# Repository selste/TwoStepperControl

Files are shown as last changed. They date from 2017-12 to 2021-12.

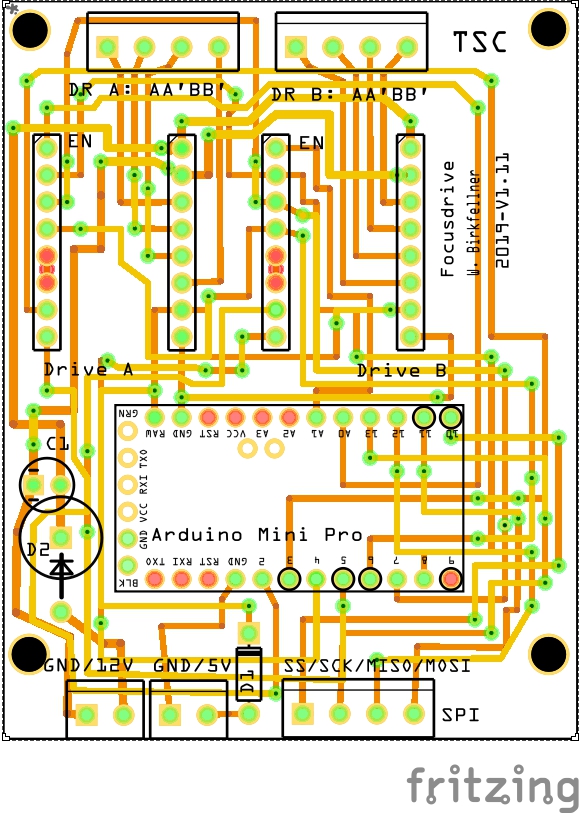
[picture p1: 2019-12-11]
Hardware/4_FocusMotors/MotorBoard_pcb.jpg

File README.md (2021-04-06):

# TwoStepperControl

## Introduction
TSC (TwinStepperControl) is a software project by Wolfgang Birkfellner and Steffen Elste to realize an open integrated control system for large and heavy astronomical telescopes. The basic idea is to use a Raspberry Pi to control a telescope and to provide basic autoguiding functionality without additional external computers. As Raspian is not an RTOS, it cannot control stepper drivers directly like a microcontroller; therefore, extra hardware is necessary which receives basic parameters (number of steps, velocity, acceleration) from the software. We are currently using AMIS 30543 bipolar driver boards with 3A maximum current per coil and a maximum voltage of 30 V.

## Features
TSC basically provides the following functionality
- Telescope tracking and GOTO using internal catalogs for german equatorial and fork mounts in the higher range - up to NEMA 34
steppers are used
- Telescope control via LX200 - both USB/Ethernet and WLAN are supported. In the absence of a WLAN-access point, TSC opens a WLAN network of its own to connect to tablets, cell phones and other computers. Namely, control via SkySafari aon iOS and Android is provided.
- Remote control via VNC (Virtual Network Clients).
- DSLR control including dithering.
- Support for two additional focuser motors.
- Free customization of drives and gears with microstepping ratios between 1/128 and 1/4.
- Image acquisition and autoguiding from guiding cameras via INDI.
- Integrated plate solving via local instalation of Astrometry.net
- Autoguiding integrated on the controller.
- ST4 is also supported

## Documentation
Because we - not intentionally - messed this up a bit in the past we're setting up a dedicated repository/site for documentation:
[TwoStepperControl Documentation](https://tscatm.wordpress.com/)
Please also take a closer look at the manual, which covers all aspects of usage and assembly. However, with the switch to the AMIS drivers, things are in motion

The [Wiki](https://github.com/selste/TwoStepperControl/wiki) in this repository will henceforth only deal with information regarding compilation (and the setup required) and related stuff.

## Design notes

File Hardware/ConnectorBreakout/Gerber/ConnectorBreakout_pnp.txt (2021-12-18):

*Pick And Place List
*Company=
*Author=
*eMail=
*
*Project=ConnectorBreakout
*Date=19:27:29
*CreatedBy=Fritzing 0.9.9b.2021-09-22.CD-348-0-f0af53a9
*
*
*Coordinates in mm, always center of component
*Origin 0/0=Lower left corner of PCB
*Rotation in degree (0-360, math. pos.)
*
*No;Value;Package;X;Y;Rotation;Side;Name
1;;;25.3563;-26.8719;0;Bottom;Hole52
2;;;11.3863;-26.8719;0;Bottom;Hole59
3;;;43.1363;-26.8719;0;Bottom;Hole33
4;;;32.9763;-26.8719;0;Bottom;Hole46
5;;;8.84633;-26.8719;0;Bottom;Hole61
6;;;54.5433;-23.1002;0;Bottom;Hole14
7;;;24.0863;-26.8719;0;Bottom;Hole49
8;;THT;34.1804;-7.35216;90;Bottom;AA' BB'2
9;;;20.3043;-42.1188;0;Bottom;Via8
10;;;57.1063;-26.8719;0;Bottom;Hole23
11;;;7.57641;-26.8719;0;Bottom;Hole60
12;;;6.30641;-26.8719;0;Bottom;Hole62
13;;;1.2265;-26.8719;0;Bottom;Hole83
14;;;36.7863;-26.8719;0;Bottom;Hole38
15;;THT;13.9033;-14.2102;90;Bottom;    
16;;;38.0563;-26.8719;0;Bottom;Hole36
17;;;20.2811;-14.2171;0;Bottom;Via16
18;;;34.2463;-26.8719;0;Bottom;Hole41
19;;;54.5663;-26.8719;0;Bottom;Hole25
20;;;3.75476;-37.0411;0;Bottom;Via6
21;;;11.3714;-37.0411;0;Bottom;Via5
22;;THT;34.2464;-42.1118;90;Bottom;   
23;;THT;34.2035;-35.2538;90;Bottom;AA' BB'
24;;;20.2811;-9.13932;0;Bottom;Via15
25;;;2.47336;-24.3702;0;Bottom;Hole15
26;;;8.82328;-20.5602;0;Bottom;Hole9
27;;THT;50.7333;-14.2102;90;Bottom;   
28;;;11.3482;-9.13932;0;Bottom;Via13
29;;THT;52.0033;-16.7502;90;Bottom;   
30;;;38.0333;-23.1002;0;Bottom;Hole12
31;;;58.3763;-26.8719;0;Bottom;Hole21
32;;;43.1779;-47.5283;0;Bottom;TXT2
33;;;48.2163;-26.8719;0;Bottom;Hole34
34;;;30.4364;-51.0018;0;Bottom;Hole4
35;;;30.4363;-26.8719;0;Bottom;Hole42
36;;;3.76641;-26.8719;0;Bottom;Hole86
37;;;30.4595;-38.2636;0;Bottom;Via11
38;;;63.4563;-26.8719;0;Bottom;Hole18
39;;THT;35.4933;-16.7502;90;Bottom;   
40;;THT;15.1964;-39.5718;90;Bottom;     
41;;;12.6563;-26.8719;0;Bottom;Hole57
42;;;55.8363;-26.8719;0;Bottom;Hole28
43;;;62.1863;-26.8719;0;Bottom;Hole19
44;;;5.03641;-26.8719;0;Bottom;Hole63
45;;;22.8163;-26.8719;0;Bottom;Hole48
46;;;49.4863;-26.8719;0;Bottom;Hole29
47;;;53.2963;-26.8719;0;Bottom;Hole24
48;;THT;14.1703;-4.81199;90;Bottom;1
49;;;2.49642;-52.2718;0;Bottom;Hole8
50;;;40.5963;-26.8719;0;Bottom;Hole40
51;;THT;34.2233;-14.2102;90;Bottom;   
52;;;46.9463;-26.8719;0;Bottom;Hole31
53;;THT;15.1733;-11.6702;90;Bottom;   
54;;THT;13.9264;-42.1118;90;Bottom;  
55;;;17.7363;-26.8719;0;Bottom;Hole58
56;;;10.1163;-26.8719;0;Bottom;Hole64
57;;;15.1963;-26.8719;0;Bottom;Hole54
58;;;52.0263;-26.8719;0;Bottom;Hole26
59;;;46.9464;-51.0018;0;Bottom;Hole2
60;;;30.4363;-10.3619;0;Bottom;Via19
61;;;41.8663;-26.8719;0;Bottom;Hole35
62;;THT;14.1934;-32.7138;90;Bottom;1
63;;;54.5664;-51.0018;0;Bottom;Hole1
64;;;50.7563;-26.8719;0;Bottom;Hole27
65;;;39.3263;-26.8719;0;Bottom;Hole37
66;;;20.2763;-26.8719;0;Bottom;Hole51
67;;THT;35.5164;-44.6518;90;Bottom;   
68;;THT;50.6904;-7.35216;90;Bottom;AA' BB'1
69;;;44.4063;-26.8719;0;Bottom;Hole32
70;;;35.5163;-26.8719;0;Bottom;Hole39
71;;;20.2764;-48.4618;0;Bottom;Hole5
72;;;2.49641;-26.8719;0;Bottom;Hole85
73;;;14.3707;-45.145;0;Bottom;TXT1
74;;;62.1864;-52.2718;0;Bottom;Hole7
75;;;21.5463;-26.8719;0;Bottom;Hole50
76;;;38.0564;-51.0018;0;Bottom;Hole3
77;;;31.7063;-26.8719;0;Bottom;Hole43
78;;;45.6763;-26.8719;0;Bottom;Hole30
79;;;62.1633;-24.3702;0;Bottom;Hole16
80;;;20.3043;-37.0411;0;Bottom;Via7
81;;;30.4133;-23.1002;0;Bottom;Hole11
82;;THT;50.7135;-35.2538;90;Bottom;AA' BB'
83;;;20.2533;-20.5602;0;Bottom;Hole10
84;;;59.6463;-26.8719;0;Bottom;Hole22
85;;;46.915;-44.6576;0;Bottom;Via9
86;;;30.4363;-16.7559;0;Bottom;Via20
87;;;3.7317;-9.13932;0;Bottom;Via14
88;;THT;50.7564;-42.1118;90;Bottom;   
89;;;8.84642;-48.4618;0;Bottom;Hole6
90;;;27.8963;-26.8719;0;Bottom;Hole45
91;;;26.6263;-26.8719;0;Bottom;Hole47
92;;;29.1663;-26.8719;0;Bottom;Hole44
93;;;46.9233;-23.1002;0;Bottom;Hole13
94;;THT;52.0264;-44.6518;90;Bottom;   
95;;;30.4595;-44.6576;0;Bottom;Via12
96;;;46.915;-38.2636;0;Bottom;Via10
97;;;46.8919;-16.7559;0;Bottom;Via17
98;;;60.9163;-26.8719;0;Bottom;Hole20
99;;;19.0063;-26.8719;0;Bottom;Hole53
100;;;13.9263;-26.8719;0;Bottom;Hole56
101;;;16.4663;-26.8719;0;Bottom;Hole55
102;;;46.8919;-10.3619;0;Bottom;Via18

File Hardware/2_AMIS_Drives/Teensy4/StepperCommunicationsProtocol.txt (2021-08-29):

Communications protocol for the Stepper Drivers of TSC
W. Birkfellner, Aug. 2021, V. 0.1

The stepperboards communicate via USB between the host computer and 
the Teensy 4.0 running the steppers with the AccelStepper library.
so far the commands are transmitted as characters, following the convention:
xyzzzzzz...
where x is a character denoting the action to be taken, y is a number between
0 and 1, and zzzzzz... is a string of bytes that is converted to a long integer. 

An example:
"a1200" sets the acceleration (denoted by 'a') of the second drive ('1' instead 
of '0') to 200 microsteps per second. 

Commands that apply to all drives (such as the request for the drive state) are given without additional bytes

In general, parameters have to be set, then the drive is enabled, and then ist should start. 
Once a motion is finished, the drive is being automatically disabled.

Command set:
0x06 or <ACK>	... responds with an identifier for the drive addressed. Replies are either "TSC_DE" or "TSC_RA". No further parameters are given.
a 		... sets acceleration in msteps/(s*s)
c 		... sets current
e 		... enables the drive; it is automatically activated when an "start drive" command (= 'o') is sent
f		... reports drive conditions. Possible parameters are
			0 = is drive moving
			1 = error on AMIS board reported
			2 = error on SPI settings
			5 = steps carried out so far
			6 = microstepping ratio
			7 = maximum speed in msteps/s 
			8 = acceleration in msteps/(s*s) 
			9 = maximum current per coil in milliAmpere
			10 = number of steps set
m 		... sets microstepping mode for a given drive: 1, 2, 4, 8, 16, 32, 64 and 128 are permitted    
o 		... engages the drive to carry out a defined number of microsteps     
r 		... resets the AMIS via its CLR pin
s 		... sets the number of steps to be carried out
v 		... sets maximum speed in msteps/s      
x 		... stops drive
z		... sets position of stepper to zero

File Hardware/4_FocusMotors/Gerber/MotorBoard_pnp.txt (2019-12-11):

*Pick And Place List
*Company=
*Author=
*eMail=
*
*Project=MotorBoard
*Date=13:08:43
*CreatedBy=Fritzing 0.9.3b.04.19.5c895d327c44a3114e5fcc9d8260daf0cbb52806
*
*
*Coordinates in mm, always center of component
*Origin 0/0=Lower left corner of PCB
*Rotation in degree (0-360, math. pos.)
*
*No;Value;Package;X;Y;Rotation;Side;Name
1;;;7.39582;-60.8985;0;Bottom;Via19
2;;;52.4807;-16.4486;0;Bottom;Via71
3;;;45.9584;-65.5036;0;Bottom;TXT2
4;;THT;9.58283;-2.85951;-90;Bottom;GND/12V
5;;;51.2107;-20.8936;0;Bottom;Via50
6;;;32.1607;-12.6386;0;Bottom;Via64
7;;;12.5126;-48.2445;0;Bottom;Via4
8;;;22.6357;-34.8635;0;Bottom;Via75
9;;;48.6707;-20.8936;0;Bottom;Via56
10;;;27.0808;-22.7985;-90;Bottom;Arduino Mini Pro
11;;;2.95082;-31.0536;0;Bottom;Via13
12;;;14.3807;-32.9586;0;Bottom;Via39
13;;;9.93582;-35.7807;0;Bottom;Via68
14;;;28.3507;-49.4685;0;Bottom;Via27
15;;THT;17.4568;-2.85951;-90;Bottom;GND/5V
16;;;42.3207;-28.5136;0;Bottom;Via47
17;;;16.9207;-58.3585;0;Bottom;Via6
18;;;46.1307;-62.1685;0;Bottom;Via44
19;;THT;4.22083;-46.9285;0;Bottom;EN
20;;;9.30082;-11.0158;0;Bottom;Via69
21;;THT;32.8238;-65.8515;-90;Bottom;DR B: AA'BB'
22;;;49.9407;-12.6386;0;Bottom;Via61
23;;;16.9207;-32.3236;0;Bottom;Via31
24;;;19.4607;-57.0885;0;Bottom;Via15
25;;;2.63332;-66.931;0;Bottom;Hole2
26;;;49.9407;-24.7036;0;Bottom;Via46
27;;;13.7397;-45.6677;0;Bottom;Via2
28;;;8.03082;-19.6236;0;Bottom;Via66
29;;THT;38.5108;-46.9285;0;Bottom;Drive B
30;;;19.4607;-41.8485;0;Bottom;Via38
31;;THT;25.8108;-46.9285;0;Bottom;EN 
32;;;5.53582;-17.0528;90;Bottom;D2
33;;;2.95082;-27.8786;0;Bottom;Via12
34;;THT;33.4588;-2.98648;-90;Bottom;SPI
35;;;46.1307;-36.1335;0;Bottom;Via24
36;;;47.4007;-34.8635;0;Bottom;Via28
37;;;28.3507;-47.5635;0;Bottom;Via30
38;;;15.0157;-55.8185;0;Bottom;Via9
39;;;51.2107;-14.8258;0;Bottom;Via73
40;;;2.31582;-62.1685;0;Bottom;Via43
41;;;51.5358;-8.07351;0;Bottom;Hole3
42;;;46.1307;-10.0986;0;Bottom;Via72
43;;;44.8607;-22.7986;0;Bottom;Via42
44;;;8.03082;-27.2436;0;Bottom;Via65
45;;;47.3698;-49.9384;-90;Bottom;TXT5
46;;;44.5785;-11.3686;0;Bottom;Via70
47;;;23.2707;-12.6386;0;Bottom;Via40
48;;;4.22082;-32.9586;0;Bottom;Via59
49;;;47.4007;-20.2586;0;Bottom;Via57
50;;;6.12582;-50.7385;0;Bottom;Via36
51;;;44.8607;-18.9886;0;Bottom;Via29
52;;THT;15.0438;-65.8515;-90;Bottom;DR A: AA'BB'
53;;;38.5107;-58.3585;0;Bottom;Via5
54;;THT;16.9496;-46.9107;0;Bottom;Drive A
55;;;44.62;-49.1489;-90;Bottom;TXT4
56;;;9.30082;-54.5485;0;Bottom;Via14
57;;;35.3357;-7.55861;0;Bottom;Via55
58;;;12.4758;-53.2785;0;Bottom;Via3
59;;;52.4807;-28.5136;0;Bottom;Via48
60;;;33.4307;-36.1335;0;Bottom;Via21
61;0.1mF;100 mil [THT, electrolytic];4.2265;-24.0437;0;Bottom;C1
62;;;23.9057;-54.5485;0;Bottom;Via33
63;;;41.0507;-32.3236;0;Bottom;Via32
64;;;37.2407;-53.2785;0;Bottom;Via18
65;;;48.6707;-22.7986;0;Bottom;Via41
66;;;37.2407;-25.3386;0;Bottom;Via51
67;;;7.39582;-48.1985;0;Bottom;Via37
68;;;15.6507;-53.9135;0;Bottom;Via11
69;;;39.7807;-25.3386;0;Bottom;Via52
70;;;13.7458;-52.0085;0;Bottom;Via1
71;;;44.8607;-59.6285;0;Bottom;Via23
72;;;49.9407;-33.5936;0;Bottom;Via45
73;;;6.12582;-54.5485;0;Bottom;Via35
74;;;35.3755;-6.81038;0;Bottom;TXT1
75;;;22.0007;-60.8985;0;Bottom;Via20
76;;;1.04582;-57.7235;0;Bottom;Via10
77;;;4.22082;-59.6285;0;Bottom;Via8
78;;;23.9057;-50.7385;0;Bottom;Via34
79;;;34.7007;-26.6086;0;Bottom;Via49
80;;;22.6357;-38.0385;0;Bottom;Via67
81;;;31.5257;-39.3085;0;Bottom;Via25
82;;;25.8107;-4.38361;0;Bottom;Via63
83;;;19.1785;-34.8635;0;Bottom;Via74
84;;;51.5358;-67.0735;0;Bottom;Hole5
85;;;36.6057;-40.5785;0;Bottom;Via26
86;;;49.9407;-17.7186;0;Bottom;Via60
87;;300 mil [THT];23.2708;-6.26311;90;Bottom;D1
88;;;2.53583;-8.07351;0;Bottom;Hole4
89;;;42.1804;-49.1414;-90;Bottom;TXT3

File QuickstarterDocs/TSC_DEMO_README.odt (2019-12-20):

TSC_DEMO.img.gz – what is it?

wbirkfellner@gmail.com – tscatm.wordpress.com

You are reading this because you apparently have received a rather big file called “TSC_DEMO.img.gz”. This is a demonstrator for the free telescope controller software TSC, written for the Raspberry Pi family of single board computers.

This is an image of a 16GB SD-card holding the minimum libraries and a binary copy of the TSC software. It is a demonstrator because all necessary tools for modifying TSC or building the hardware associated with it were removed for saving space. Without the hardware, TSC is a brain without limbs, and therefore its functionality is very limited.

Things that can be done:

- Get an idea of the internal functionality of TSC.
- See how TSC integrates into your local network/WLAN.
- Check how it connects to your favourite planetarium program. Denote that a serial connection via USB is only available with the TSC hardware, but connection via WLAN (e. g. via SkySafari or Kstars) is possible. Of course TSC does not move, but if you Sync on an object using the internal catalog, you can at least see little crosshairs hopping around.
- Check whether your camera connects to the internal camera interface of TSC for use with the internal guider or (in the near future) internal platesolving, a functionality under development for use with the new Raspberry Pi 4 family of SBCs.

How to make an SD card:

- Uncompress the TSC_DEMO.img.gz image. Make sure that you have enough space available on your harddisk, and yes, this takes a while. On Linux, you can simply double-click TSC_DEMO.img.gz. On other operating systems, the procedure is similar.
- Make a physical copy on a (fast) 16 GB minimum SD card. On Linux (or Raspian), this is done by typing: sudo dd if=<location of input file> of=<device to write to> bs=8M status=progress <device to write to> is the physical location of your SD-card; with an external card reader, this is usually a /dev/sd… device, an internal card reader can often be found at /dev/mmcblk0. You can also use the Disk Image Writer that comes for instance with Ubuntu. Writing an SD-card is of course also feasible on other operating systems; for details, check for instance: https://learn.sparkfun.com/tutorials/sd-cards-and-writing-images/all
- Put the SD card into at least a Raspberry Pi 3B, connect a mouse and a HDMI monitor and boot it.
- Synchronize your clock, either by using SkySafari (sse instructions below), or by connecting your Raspberry Pi to an Ethernet cable and wait until a time server signal is received. You can also set date and time manually by closing TSC using the Exit button, opening a terminal by pressing <Ctrl-Alt-T> and typing: sudo date -s "20 DEC 2019 18:00:00" – of course with the right time and date. Restart TSC with the TSC desktop icon after that.

What you will see:

- A warning that no drives are connected. This is ok as no drives are connected.
- After confirmation, TSC will come up. It spawns an autonomous network called TSCHotspot; the password is TSCRaspi – use these credentials to access the LX200 client client via your planetarium program. The IP address to connect to is 192.168.50.5, the Port is 49152. Set your location in the Location tab, store it using Store Data and make sure that your system clock is correct – the TSC hardware has a buffered real-time clock, you don’t have one. On SkySafari, you can synchronize by sending time and location; make sure that the checkbox Allow time/position from LX200 is checked in the Location tab of TSC.
- Plug in your camera and go to the CCD tab. Select your camera vendor, click Start INDI Server and Connect. In the next tab (called Guiding), you can now Expose an image an see whether something comes in there.

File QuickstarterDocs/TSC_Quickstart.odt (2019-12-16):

Starting with TSC – the bare minimum guide

W. Birkfellner, wbirkfellner@gmail.com

tscatm.wordpress.com

Let us assume that the TSC hardware is assembled and powered up – so here is a very short and minimalistic guide to get started with TSC.

1: Connect your drives

TSC operates bipolar stepping motors. These have two coils and four wires running out. Some have more, and then reading the documentation for the drives is recommended. Let us call the wire pairs AA’ and BB’. In order to find out which wires form a pair, one needs a documentation or a multimeter. A pair of wires always has a relative resistance of almost 0 Ohm. Connect these pairs to the terminals on the driver boards. If you figure out at a later stage that your drives are turning in the wrong direction, you may need to permutate A and A’ or B and B’ - or both. Fig. 1 shows the location of the terminal on the AMIS board.

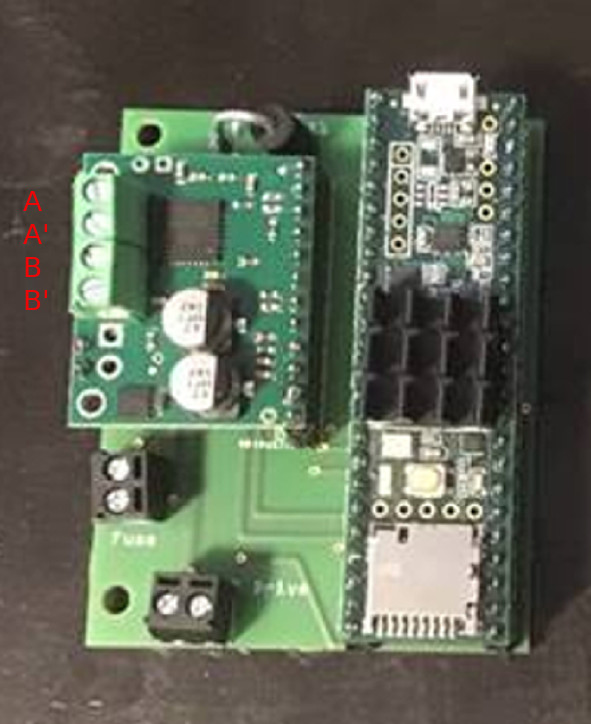
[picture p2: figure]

| Fig. 1: Connection terminals for the four wires of a bipolar stepper on one of the AMIS boards. This is an older board with a Teensy 3.5 as a microcontroller.

2: Set up current and gear ratios:

TSC can handle up to 3A per coil and a motor voltage up to 30V (the latter affects the maximum end speed). Your motor also has a maximum current rating. Do not set the current above 70% of this rating (for the time being). Fig. 2 shows how to adjust the current in the Settings dialog of TSC for both the right ascension (RA) and Declination drive. Also set an acceleration A in microsteps/second². 5000 msteps/s² is a good starting point. Set the gear and microstepping ratios and press Store gear data. A recommended setting for microsteps is 1/128 for Track and Guide, 1/16 for Move and 1 /4 for GoTo. Uncheck Northern Hemisphere if you are on the southern hemisphere. Leave Enable Meridian Flip disabled, even if you have a German equatorial, for the time being.

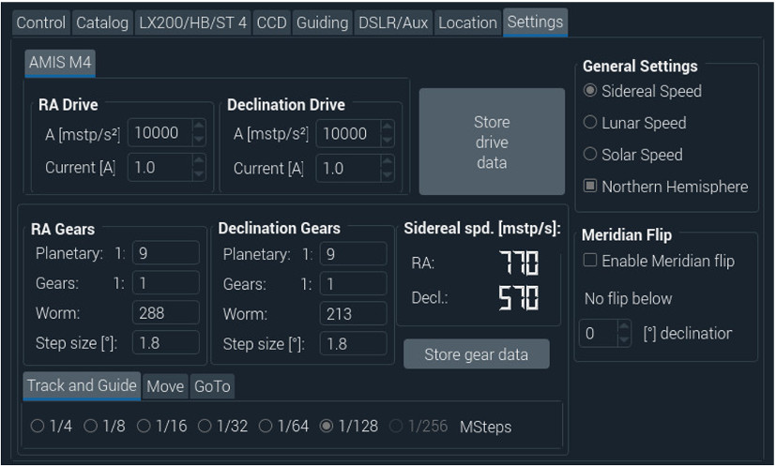
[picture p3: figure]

Fig. 2: Adjustment of current, gears and microsteps for basic stepper operation. Start with 70 % of your rated stepper coil current. A value of 5000 microsteps/s² is a good value for the acceleration A of the steppers. Press Store drive data once you have found your settings. Leave the Enable Meridian Flip check box unchecked for the time being. Enter the gear ratio for you Planetary drive, your intermediate Gear (e. g. belts) and the number of teeth on you Worm wheel. Also enter the step size for a full step and the microstepping ratios for Tracking and Guide-ing, handbox Moves and GoTo. Press the Store gear data button once you are done.

3: Set up speeds and do fine adjustments:

Now, your mount should be ready for first moves using the direction buttons on the main screen (Fig. 3). Set V-Move to 50 (multiples of sidereal speed) and V-GoTo to 100. Press the Store Speeds button. Move the drives with Up, Down, Left and Right. Now fine adjust currents and maximum speed. A whining sound at maximum speed accompanied by no motion means that the speed is too high for this setup – reduce it. A rough motion of the drive, accompanied with heating the drive up, means that the current is to high – lower it. An irregular motion, accompanied by crackling sounds, means that the torque is too low and the motor loses steps – increase the current, but not beyond the maximum rating of the drive. An optimal setting is found when the drives operate quietly with the minimum current needed. Repeat this until the mount moves smoothly. Also check the maximum GoTo speed V-GoTo by setting V-Move to the same value – and always Store Speeds.

4: Check directions

Grossly point your scope to the south horizon using a level and a compass; if you have a German equatorial, make sure that it’s position (left or right of pier) is also indicated in the GEM left of pier checkbox (Fig. 3). Make sure that the hemisphere you are on (north or south) is indicated properly in the Settings (Fig. 1). If a press on the Right button moves the scope left (or if Up and Down are reversed) – go back to 1.) and permutate A with A’ or B with B’ or both.

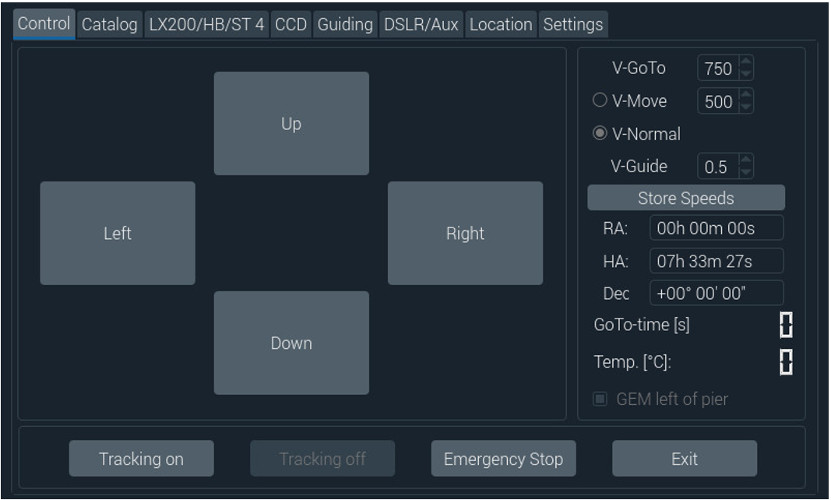
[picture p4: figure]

| Fig. 3: The main screen – adjust your desired speeds for motion (V-Move) and GoTo (V-GoTo) and fine tune your motor current. Don’t forget to Store Speeds if you changed them. The speed is selected with the radiobuttons left of V-Normal and V-Move. The direction buttons are latching – press them a second time to stop a motion. If you cannot enter a current or set a speed, then the drive or speed is active. Use Tracking off button to stop the mount compensating Earth’s rotation if you want to edit the RA-drive settings. Uncheck V-Move to change the speed.

5: Enable meridian flip (if needed)

If you have a German equatorial (GEM), point your scope to the south horizon, make sure that the scope position left/right of the pier matches the GEM left of pier checkbox (Fig. 3) and Enable the Meridian flip in the Settings tab (Fig. 2). Set No flip below to the minimum declination visible from your site (e. g. -42° if you are at a latitude of 48° as shown in Fig. 4).

6: Sync the scope

Make sure your clock is set up properly and your location is entered correctly (Fig. 4).

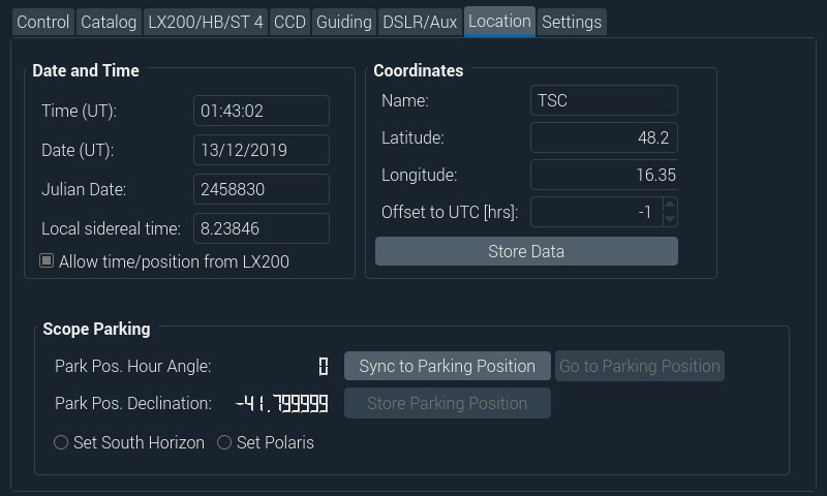
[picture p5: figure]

| Fig. 4: Set your location and make sure that the time (Universal time zone) is set correctly, or let SkySafari do this for you (in this case, the Allow time/position from LX200 checkbox needs to be checked). Don’t forget to Store the Data. If your scope is approximately looking to the south horizon, check Set South Horizon and press the Sync to Parking Position button. If you have not set your time yet and you don’t have SkySafari – connect your Raspberry Pi to a network via Ethernet and wait for an incoming time server signal.

Position your scope to the south horizon grossly using a compass and a level using the direction buttons (Fig. 3) as indicated in Section 4. Set the parking position to the South Horizon in the Location tab and Sync to this Parking Position. Your scope is now approximately synced. Identify a nearby bright star and go to the Catalog tab using the PreciseAlignmentStars or the BrightStars catalogue, click its name and press GoTo (Fig. 5).

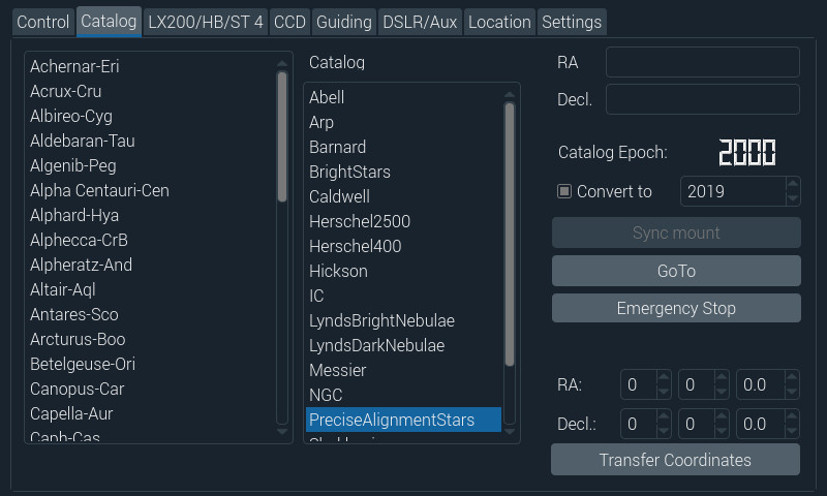
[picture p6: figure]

| Fig. 5: Precise syncing using a bright star and the BrightStars or the PreciseAlignmentStars catalog. Select a star you want to sync on and press GoTo. Fine align the star in the scope using a low to medium power eyepiece and the direction buttons (Fig. 3). Once the star is in the center of the eyepiece, press Sync mount again.

GoTo this bright star and locate it in the eyepiece or finder precisely by fine tuning the scope position with the direction buttons; once it is in the center of the eyepiece of your telescope, Sync the mount again. The scope should now perform GoTo-slews precisely if it is well aligned. Of course these steps can also be carried out through a planetarium program like Kstars.

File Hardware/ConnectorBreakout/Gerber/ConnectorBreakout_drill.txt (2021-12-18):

; NON-PLATED HOLES START AT T1
; THROUGH (PLATED) HOLES START AT T100
M48
INCH
T1C0.039370
T2C0.118110
T100C0.038000
T101C0.039370
T102C0.015748
T103C0.040000
%
T1
X000482Y010579
X011982Y010579
X016982Y010579
X004982Y010579
X008982Y010579
X005482Y010579
X009482Y010579
X024482Y010579
X010982Y010579
X012482Y010579
X003982Y010579
X009982Y010579
X022482Y010579
X006982Y010579
X000982Y010579
X015482Y010579
X019482Y010579
X017982Y010579
X022982Y010579
X021482Y010579
X014482Y010579
X008482Y010579
X016482Y010579
X021982Y010579
X018982Y010579
X017482Y010579
X001482Y010579
X012982Y010579
X013482Y010579
X020982Y010579
X023482Y010579
X007982Y010579
X011482Y010579
X002482Y010579
X004482Y010579
X024982Y010579
X006482Y010579
X007482Y010579
X002982Y010579
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

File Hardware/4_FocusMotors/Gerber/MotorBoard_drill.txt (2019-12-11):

; NON-PLATED HOLES START AT T1
; THROUGH (PLATED) HOLES START AT T100
M48
INCH
T100C0.015748
T101C0.038000
T102C0.040000
T103C0.035000
T104C0.042000
T105C0.129921
%
T100
X013161Y014225
X008661Y023975
X006161Y021225
X006661Y012725
X020661Y006475
X007550Y013725
X009411Y021475
X002411Y021475
X000411Y022725
X011161Y018725
X020661Y011225
X003161Y010725
X003161Y007725
X007661Y022475
X013911Y002975
X000911Y024475
X002911Y023975
X019661Y009725
X014661Y009975
X001661Y012975
X020161Y008225
X004926Y018993
X001161Y010975
X004911Y020975
X017661Y007475
X005911Y021975
X005661Y012975
X020161Y005836
X008911Y013725
X008911Y014975
X019161Y008975
X012661Y004975
X016661Y011225
X001661Y023475
X015161Y022975
X005409Y017979
X002411Y019975
X018161Y003975
X018161Y024475
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

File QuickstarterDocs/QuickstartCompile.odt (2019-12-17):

How to compile TSC

W. Birkfellner

wbirkfellner@gmail.com

Let us assume you have a recent SD-card in the developer version – that is with all software installed for programming and building TSC; and let us assume that you have at least a Raspberry Pi 3 B+, as compiling the C++-sourcecode can be cumbersome.

- Download all data from https://github.com/selste/TwoStepperControl
- Go to you Downloads folder and extract the .zip file to /home/pi
- Open TwoStepperControl-master/C++Source/qdarkstyle and
- right-click rc.tar and select Extract here – see also Fig. 1. A new folder rc should become visible. These are the resources for the stylesheet defining the user interface
- Open TwoStepperControl.pro by double clicking it in TwoStepperControl-master/C++Source/. QtCreator will be invoked.
- Select Release and click on Build › Build project “TwoStepperControl”
- Ignore all warnings and wait until the compilation process is done as indicated by the progress bar in the lower right hand side. (Fig. 2).
- Go one directory up to TwoStepperControl-master/ and copy the Catalogs folder to the build-TwoStepperControl-Desktop-Release folder (Fig. 3).
- TSC can be started by double clicking the TSC icon on the desktop.

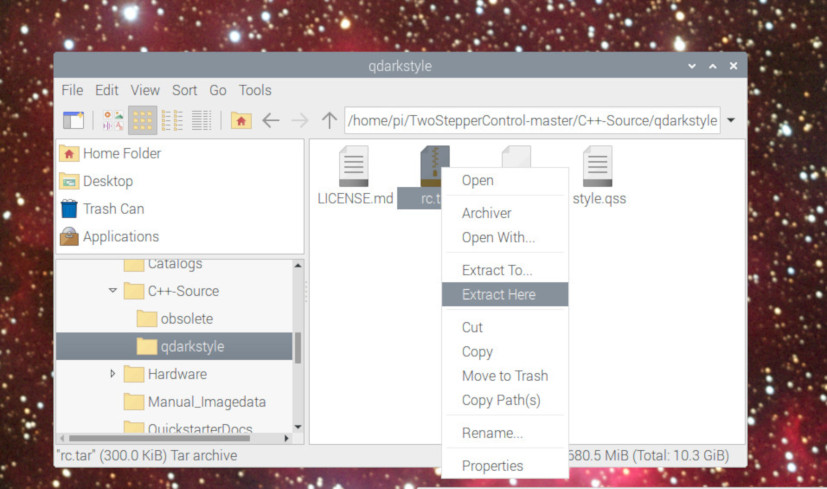
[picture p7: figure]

| Fig. 1: Extraction of the rc-folder from rc.tar – a new folder named rc will appear.

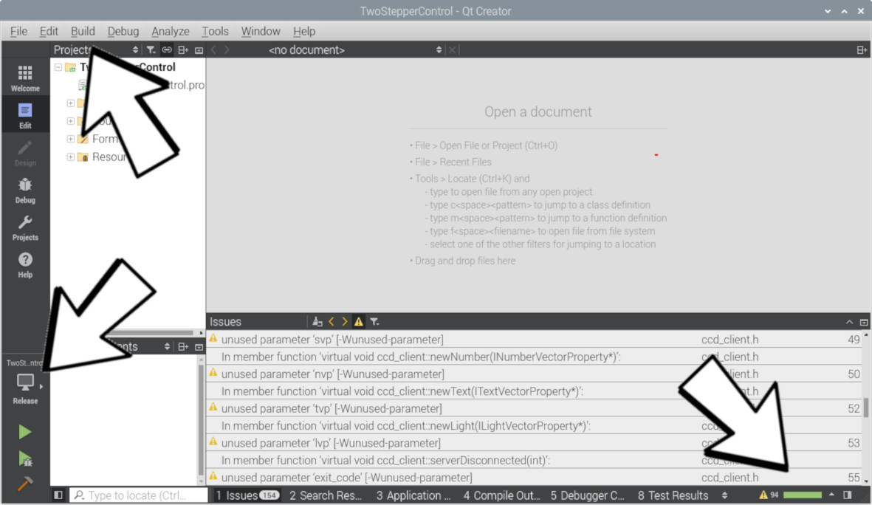
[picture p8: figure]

| Fig. 2: Compilation with QtCreator. Open TwoStepperControl.pro in the C++Source folder and take care that you are in Release mode (lower left hand) and start the compilation process in the Build menu.

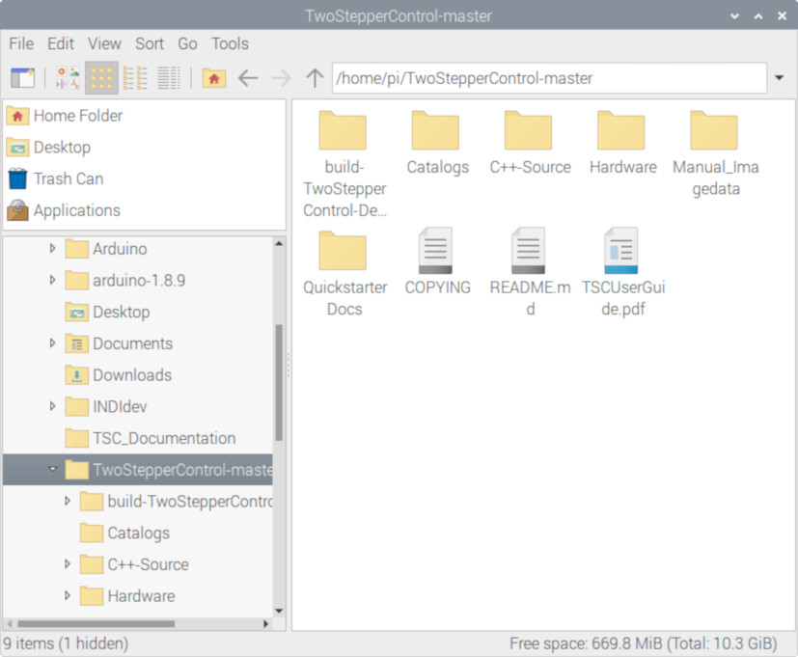
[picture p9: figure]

| Fig. 3: Copy the Catalogs folder to build-TwoStepperControl-Desktop-Release.

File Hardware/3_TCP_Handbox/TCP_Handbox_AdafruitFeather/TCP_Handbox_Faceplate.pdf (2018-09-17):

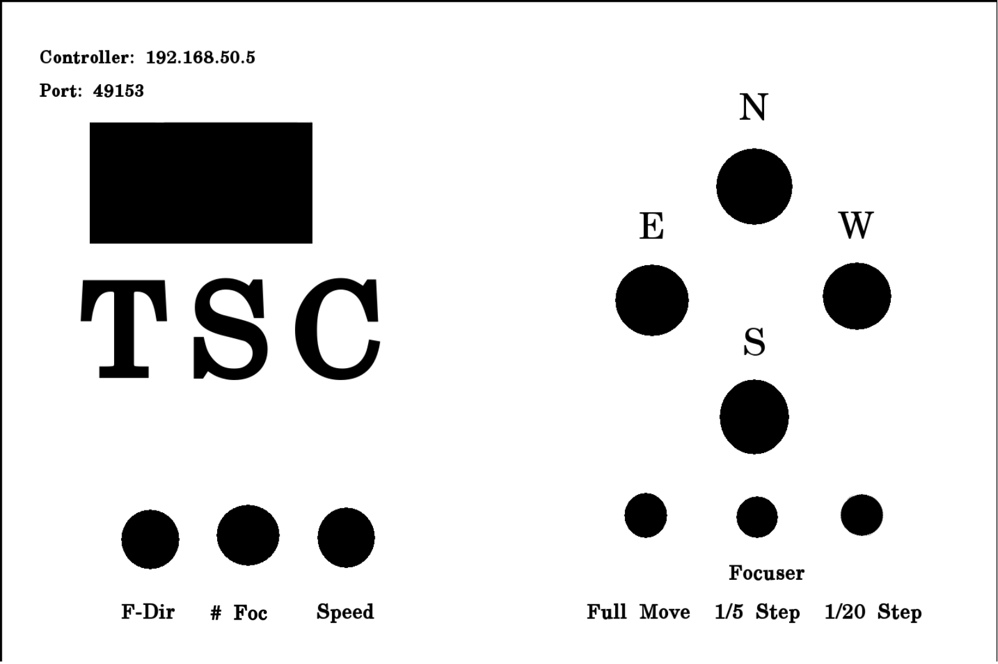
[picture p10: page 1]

# Foc

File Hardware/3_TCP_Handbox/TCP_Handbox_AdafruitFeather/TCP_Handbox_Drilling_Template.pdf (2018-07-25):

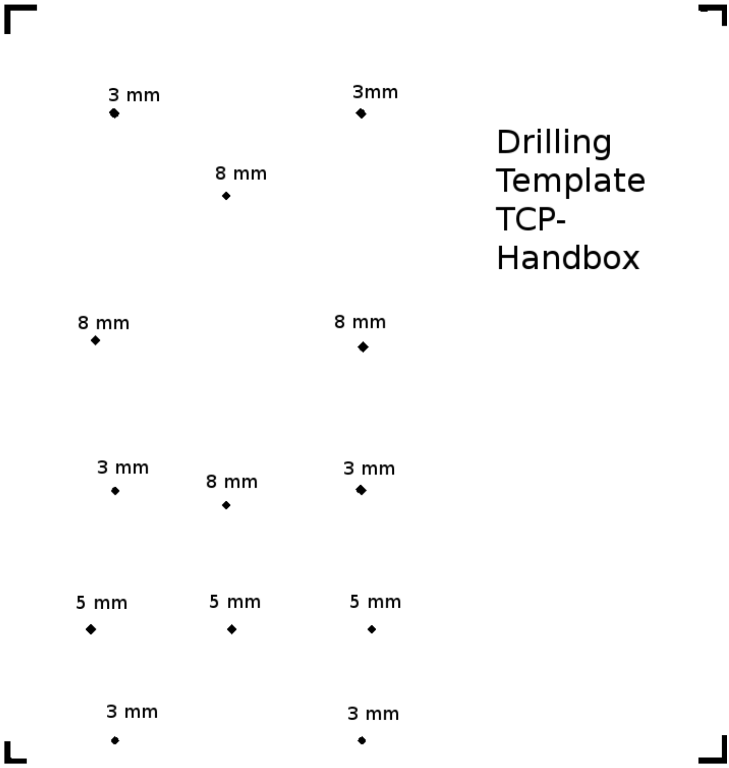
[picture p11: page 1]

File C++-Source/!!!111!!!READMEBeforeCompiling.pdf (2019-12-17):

### How to compile TSC

W. Birkfellner
wbirkfellner@gmail.com

Let us assume you have a recent SD-card in the developer version – that is with all software installed for programming and building TSC; and let us assume that you have at least a Raspberry Pi 3 B+, as compiling the C++-sourcecode can be cumbersome.
- Download all data from https://github.com/selste/TwoStepperControl
- Go to you Downloads folder and extract the .zip file to /home/pi
- Open TwoStepperControl-master/C++Source/qdarkstyle and
- right-click rc.tar and select Extract here – see also Fig. 1. A new folder rc should become visible. These are the resources for the stylesheet defining the user interface
- Open TwoStepperControl.pro by double clicking it in TwoStepperControl-master/C+ +Source/. QtCreator will be invoked.

### - Select Release and click on Build › Build project “TwoStepperControl”

- Ignore all warnings and wait until the compilation process is done as indicated by the progress bar in the lower right hand side. (Fig. 2).
- Go one directory up to TwoStepperControl-master/ and copy the Catalogs folder to the build-TwoStepperControl-Desktop-Release folder (Fig. 3).
- TSC can be started by double clicking the TSC icon on the desktop.

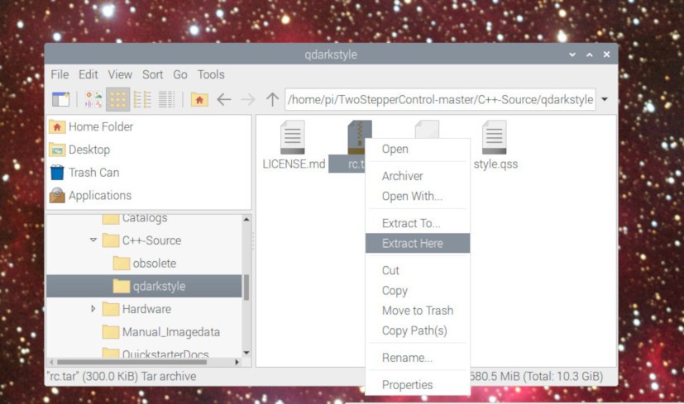
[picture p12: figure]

Fig. 1: Extraction of the rc-folder from rc.tar – a new folder named rc will appear.

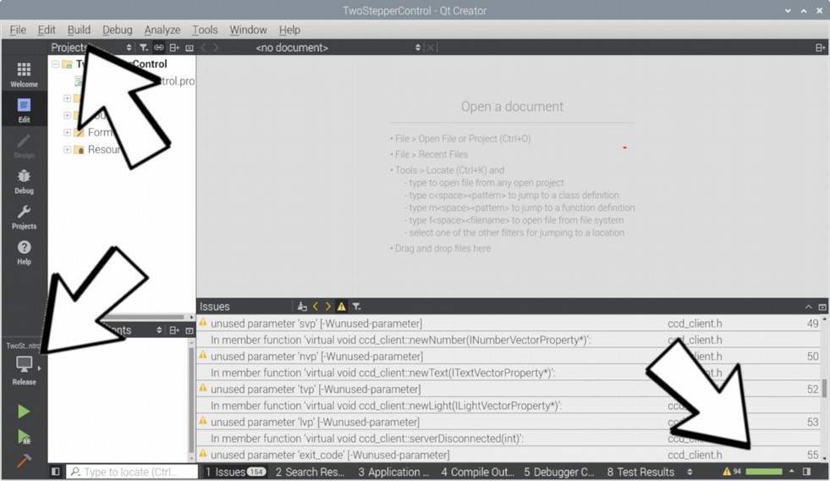
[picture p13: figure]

Fig. 2: Compilation with QtCreator. Open TwoStepperControl.pro in the C++Source folder and take care that you are in Release mode (lower left hand) and start the compilation process in the Build menu.

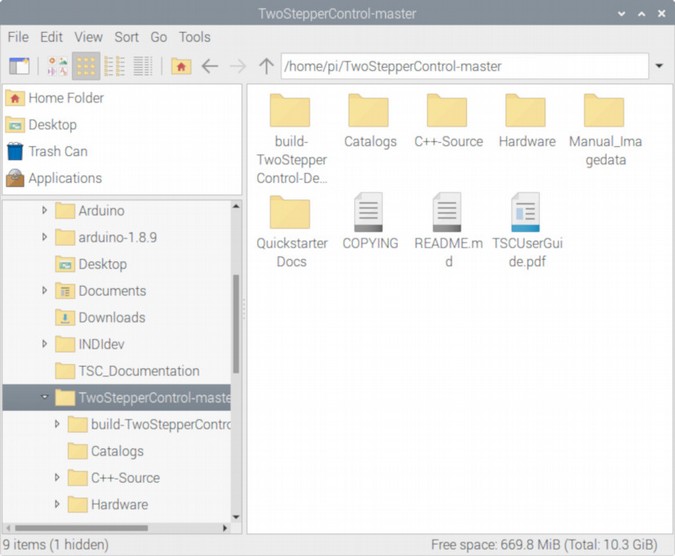
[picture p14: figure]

Fig. 3: Copy the Catalogs folder to build-TwoStepperControl-Desktop-Release.

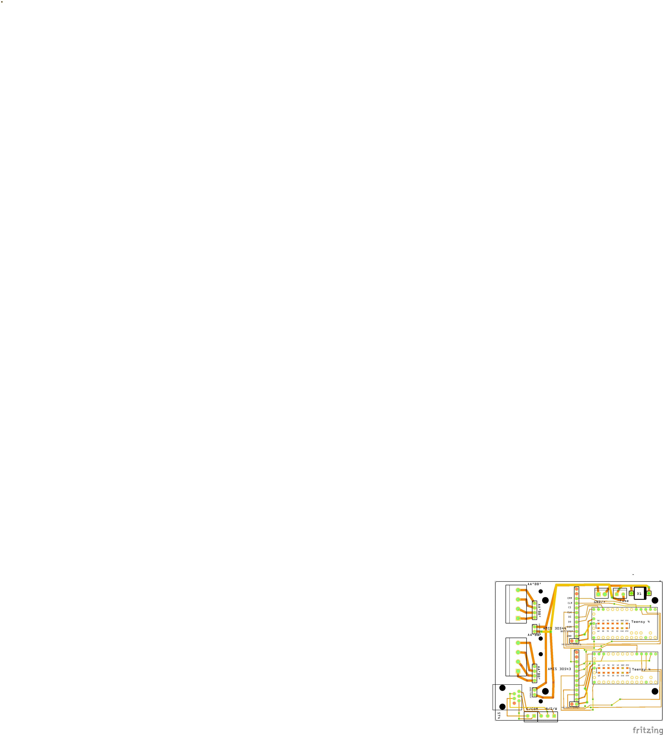
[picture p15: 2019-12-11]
Hardware/2_AMIS_Drives/Teensy4/AMIS30543_Teensy_2_pcb.jpg

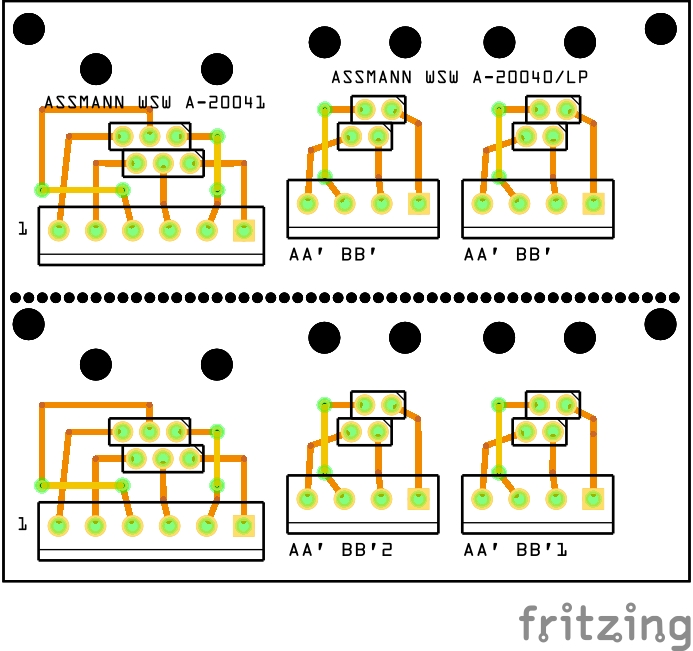
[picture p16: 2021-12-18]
Hardware/ConnectorBreakout/ConnectorBreakout_pcb.jpg

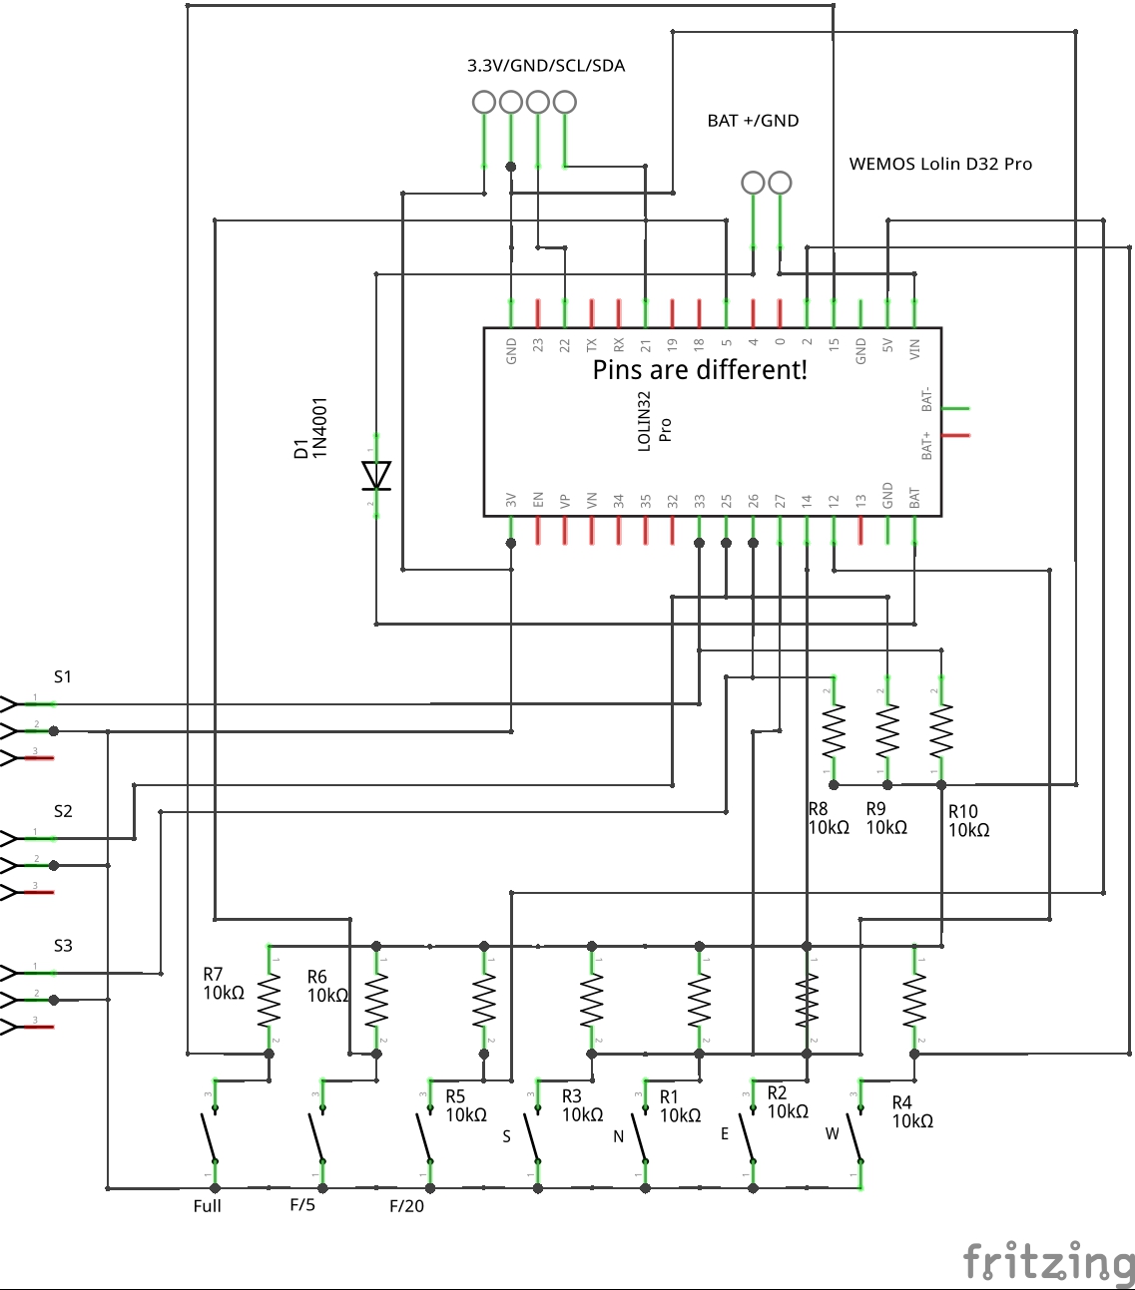
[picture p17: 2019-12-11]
Hardware/3_TCP_Handbox/TCP_Handbox_LOLIND32Pro/TCP_Handbox_schem.jpg

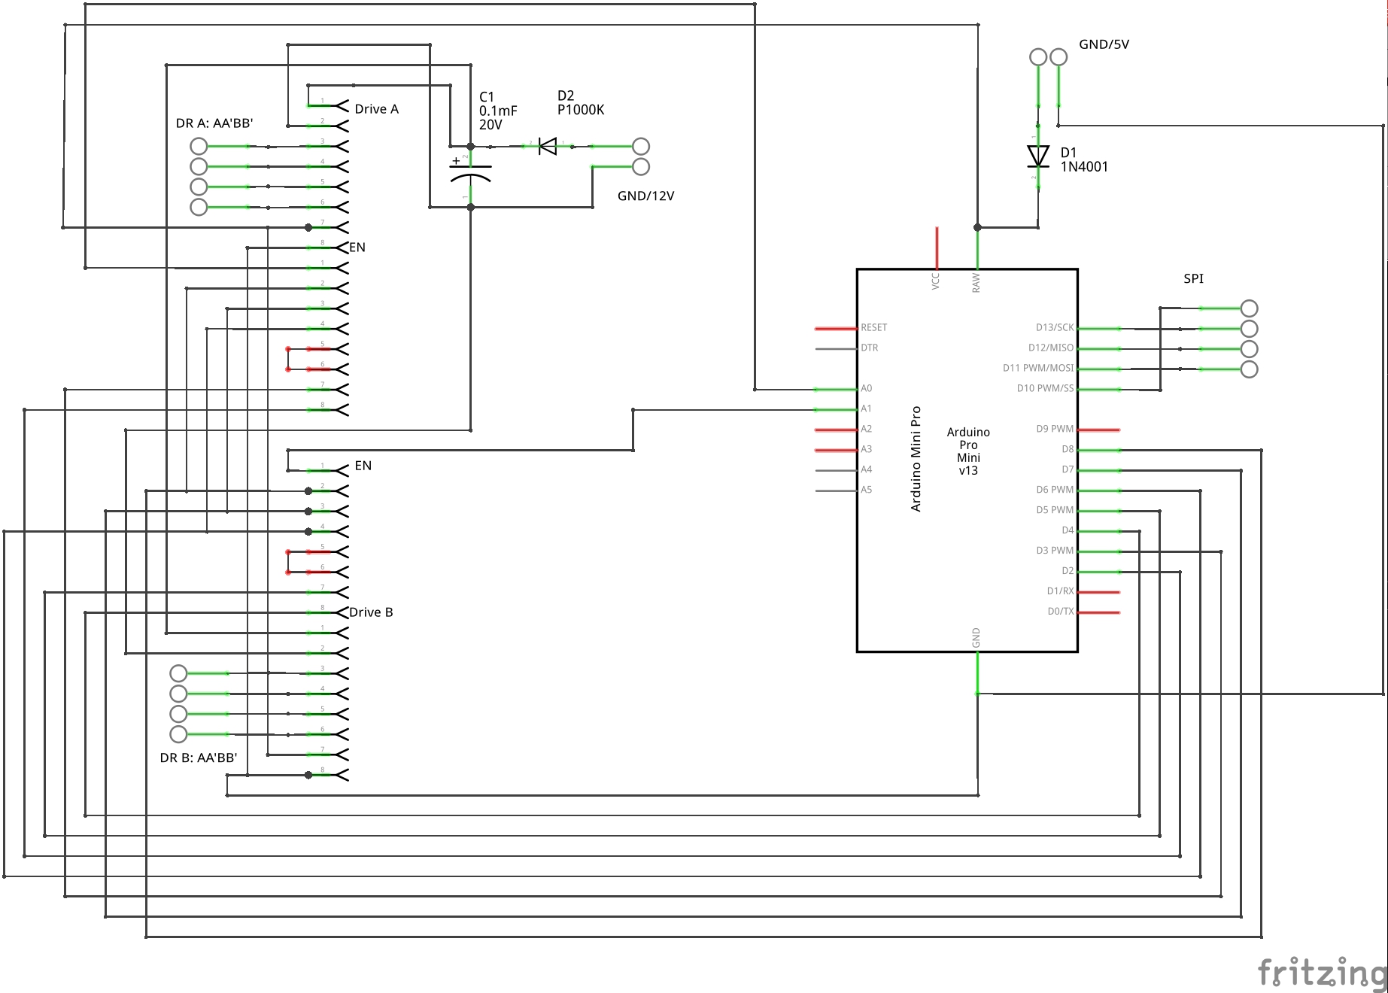
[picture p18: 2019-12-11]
Hardware/4_FocusMotors/MotorBoard_schem.jpg

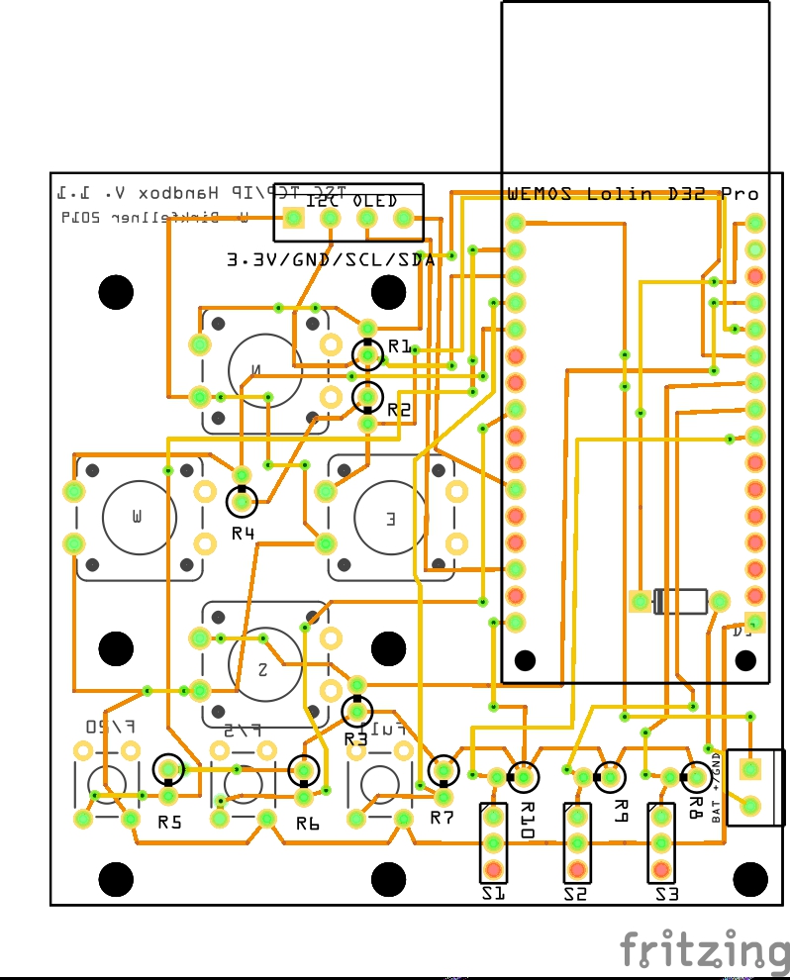
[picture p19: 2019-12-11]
Hardware/3_TCP_Handbox/TCP_Handbox_LOLIND32Pro/TCP_Handbox_pcb.jpg

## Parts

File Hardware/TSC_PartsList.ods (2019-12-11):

Parts List TSC – from www.conrad.at, www.exp-tech.de, eckstein-shop.de | Article-No. | Seller | Cost (€) | Article# by Producer | Producer
For programming the ST4 module and the focus driver, one needs this (but the same is used on the HAT):
Adafruit CP2104 USB/Serial Converter | EXP-R15-1157 | ExpTech | 6.45 | 3309 | Adafruit
Focus driver DRV 8825/A4988 version (optional)
Arduino Mini Pro 16 MHz, 5V | AR01011 | Eckstein Components | 4.95 |  | Eckstein
Polulu DRV8825 (2x), alternatively the A4988 | EXP-R25-004 | Exp-Tech | 15.3 | 2133 | Polulu
Connector, 2 contacts, 3.5 mm RM (2x) | 567588-62 | Conrad | 0.68
Connector, 3 contacts, 3.5 mm RM (1x) | 567615-62 | Conrad | 0.5
Connector, 4 contacts, 3.5 mm RM (3x) | 732154-62 | Conrad | 1.44
Elko, 0.1 mF, 50 V, 5 mm RM | 445288-62 | Conrad | 0.28 |  |  | Total (without PCB):
IN4007 – Diodes D1 and D2 | 162272-62 | Conrad | 0.2 |  |  | 23.35
WLAN-Handbox (optional)
10 kOhm Resistors (10x) R1-R10 | 1417569 | Conrad | 1.2
4 Tactile Switches | EXP-R05-243 | Exp-tech | 2.2 | COM-09190 | SparkFun
3 Tactile Switches | EXP-R05-027 | Exp-Tech | 1.2 | COM-00097 | SparkFun
3 On/OffSwitch | 701147 | Conrad | 3.03 | 805 | Adafruit
1 On/Off Switch | PO1406 | Eckstein Components | 0.75
Connector, 4 contacts, 3.5 mm RM (1x) | 732154-62 | Conrad | 0.48
Connector, 3 contacts, 3.5 mm RM (2x) | 567615-62 | Conrad | 1
LOLIN D32 PRO V. 2, Wemos | EXP-R12-171 | Exp-Tech | 15.95 |  | WEMOS
Lithium-Ion Polymer Batterie 3,7V 2500mAh JST-PH Connector | ZB07008 | Eckstein Components | 8.45 | LP785060 |  | Total (without PCB and case)
1.3” I2C OLED display, SSH1106, 128x64 pixels | SER00217 | semaf.at | 12 € |  |  | 34.26
Case is arbitrary
Raspberry Pi Hat & Pi
Raspberry Pi 3 Model B | EXP-R12-118 | Exp-Tech | 38.9 | RASPBERRYPI-3-MODB-1GB | Raspberry Pi Found
Adafruit DS 3231 HW-Clock | EXP-R15-927 | Exp-Tech | 14.95 | 3013 | Adafruit
Adafruit CP2104 USB/Serial Converter | EXP-R15-1157 | ExpTech | 6.45 | 3309 | Adafruit
Cooling bodies for Pi | EXP-R12-016 | Exp-Tech | 4.2
Fan for Pi | EXP-R15-1200 | Exp-Tech | 3.95 | 3368 | Adafruit
40 Pin Extra Tall Header | 485-1992 | Mouser | 6.38 | 1992 | Adafruit
16 GB SD-Card |  |  | 12
Arduino Mini Pro 5V 16 MHz | AR01011 | Eckstein Components | 4.95 | DEV-11113 | SparkFun
12V-5V Step down converter | CP06082 | Eckstein Components | 8.95
BC 547 (2x) | 154709 | Conrad | 0.44
Connector, 3 contacts, 3.5 mm RM (2x) | 729990 | Conrad | 1
Connector, 2 contacts, 3.5 mm RM (1x) | 729981 | Conrad | 0.34
Connector, 5 contacts, 3.5 mm RM (1x) | 732166 | Conrad | 0.42
Connector, 4 contacts, 3.5 mm RM (2x) | 732154 | Conrad | 1
ILD 74 Optocoupler | 153533 - 62 | Conrad | 1.2
Pins | 741333 - 62 | Conrad | 3.09
Resistor 220 Ohm, 2x (R5 – R6) | 423289 | Conrad | 1.16
Resistor 118 kOhm, 4x (R7 – R10) | 423610 | Conrad | 2.32
Resistor 470 Ohm, 1x (R1) | 423327 | Conrad | 0.58
Resistor 1 kOhm, 1x (R2) | 423360 | Conrad | 0.58
Resistor 4.7 kOhm, 2x (R3,R4) | 423440 | Conrad | 1.16
IN4007 – Diode D1 | 162272-62 | Conrad | 0.1
Distance 20 mm (3x) | 526657 | Conrad | 1.32
USB-Breakout | EXP-R15-708 | Exp-Tech | 4.35 |  | Adafruit
2.5 mm DSLR Jack | 738581 | Conrad | 2.19
3.5 mm Stereo Jack | 738619 | Conrad | 2.09
Adafruit TM36 | EXP-R15-744 | Exp-Tech | 1.65 |  | Adafruit
3.5 mm Stereo Plug | 738543 | Conrad | 3.29
RJ 12 Jack | 1401816 | Conrad | 0.69
Female Header (2x) | 733755 | Conrad | 3.58
800x480 Touchscreen HDMI Display 5” or similar (optional) | WS40016 | check Eckstein Components | 42,99
Tactile Switch | EXP-R05-027 | Exp-Tech | 0.4 | COM-00097 | SparkFun | Total (without PCB): | EXP-R05-027 | Exp-Tech | 1.2 | COM-00097 | SparkFun | 3 Tactile Switches | EXP-R05-027 | Exp-Tech | 1.2 | COM-00097 | SparkFun | 3 Tactile Switches | EXP-R05-027 | Exp-Tech | 1.2 | COM-00097 | SparkFun | 3 Tactile Switches | EXP-R05-027 | Exp-Tech | 1.2 | COM-00097 | SparkFun | 3 Tactile Switches | EXP-R05-027 | Exp-Tech | 1.2 | COM-00097 | SparkFun | 3 Tactile Switches | EXP-R05-027 | Exp-Tech | 1.2 | COM-00097 | SparkFun | 3 Tactile Switches | EXP-R05-027 | Exp-Tech | 1.2 | COM-00097 | SparkFun | 3 Tactile Switches | EXP-R05-027 | Exp-Tech | 1.2
 |  |  |  |  |  | 133.68
Stepper Drivers
Polulu AMIS 30543, 2x | EXP-R25-466 | Exp-Tech | 37.88 | 2970 | Pololu
Teensy 4.0, 2x | EXP-R05-1290 | Exp-Tech | 42.24 | Teensy 40
Fuse Holder 5x20, 2x | 1588080 | Conrad | 2.58
Power Diode 1N5404, 2x | 162400 | Conrad | 0.4 |  |  | Total (without PCB):
 |  |  |  |  |  | 83.1
PO1406
Missing: Housing, Power Supply, PCBs
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

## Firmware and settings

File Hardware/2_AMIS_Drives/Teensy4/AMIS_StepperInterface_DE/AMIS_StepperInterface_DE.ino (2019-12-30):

// sketch for controlling an Pololu AMIS 30543 stepper controller board with a Teensy 4 microcontroller.
// wolfgang birkfellner, 2018. wbirkfellner@gmail.com
// this is the RIGHT ASCENSION drive

#include <SPI.h>
#include <AMIS30543.h>
#include <AccelStepper.h>
#include <stdlib.h>

const uint8_t amisDirPin = 2;
const uint8_t amisStepPin = 1;
const uint8_t amisSlaveSelect = 10;
const uint8_t amisErrPin = 3;
const uint8_t resetPin = 0;

AMIS30543 stepper;
AccelStepper accelStepper(AccelStepper::DRIVER, amisStepPin, amisDirPin);

struct kinematicParametersStruct {
  long steps;   // number of steps to be carried out
  long stepsDone; // steps done at the time being
  long maxSpeedInMicrosteps; // maximum speed in msteps/s
  long acceleration; // acceleration in msteps/s
  bool isActive; // flag whether the drive is moving
  uint16_t current; // maximum current per coil given in milliAmpere
  uint8_t stepMode; // microstepping ratio: 1, 2, 4, 8, 16, 32, 64 or 128 
};

struct kinematicParametersStruct driveParams;
char commandIdentifier; // the command syntax is a character followed by a numerical value
char usbCommand[64]; // command received via usb; maximum size is 64 bytes
char outputString[64]; // a string holding the answer
String outputFloat;

//------------------------------------------------------------
void setup() {
  SPI.begin(); // start SPI for setting up the AMIS board
  stepper.init(amisSlaveSelect); // initialize the AMIS board while giving the SPI slave select line
  delay(5);
  Serial.begin(10000000); // communication is native USB - speed is set to maximum 10 Mbit/s should be ok  

  driveParams.steps = 20000; // default parameters
  driveParams.stepsDone = 0;
  driveParams.maxSpeedInMicrosteps = 1000;
  driveParams.acceleration = 1000;
  driveParams.isActive = false;
  driveParams.current = 800;
  driveParams.stepMode = 16;

  accelStepper.setMaxSpeed(driveParams.maxSpeedInMicrosteps);
  accelStepper.setAcceleration(driveParams.acceleration);
  accelStepper.setCurrentPosition(0); // initialising the accelstepper library
  
  stepper.resetSettings();
  stepper.setCurrentMilliamps(driveParams.current);
  stepper.setStepMode(driveParams.stepMode); // setting the AMIS parameters via SPI
  stepper.enableDriver(); 
}

//------------------------------------------------------------
void loop() {
  long numVal, charsAvailable, chCounter;

  accelStepper.run(); // buffer motion parameters for the stepper
  charsAvailable=Serial.available(); // check USB input
  if (charsAvailable != 0) {  // got a string via USB
    accelStepper.run();
    commandIdentifier=Serial.read(); // the first character is the command identifier
    charsAvailable--;
    if (charsAvailable != 0) {
      for (chCounter = 0; chCounter <= charsAvailable; chCounter++) {
        usbCommand[chCounter]=Serial.read();
      }
      usbCommand[chCounter+1]='\0';
    } // assemble a numerical value from the remainder of the input
    numVal = strtol(usbCommand, NULL, 10);
    accelStepper.run();
    switch (commandIdentifier) {
    case 0x06: // ACK ... responds with an identifier for the drive addressed
      replyWithDriveID(); 
      break;
    case 'a': // set acceleration in msteps/(s*s)
      setAcc(numVal);   
      break;
    case 'c': // set current
      setCurrent(numVal);      
      break; 
    case 'e': // enable the drive; it is automatically activated when an "start drive" command (= 'o') is sent
      enableDrive(numVal); 
      break;
    case 'f':
      reportAMISStates(numVal); // report conditions. 0 = is drive moving, 1 = error on AMIS board reproted, 2 = error on SPI settings, 5 = steps carried out at the given time,  
      break;                    // 6 = microstepping ratio, 7 = maximum speed in msteps/s, 8 = acceleration in msteps/(s*s), 9 = maximum current per coil in milliAmpere, 10 = number of steps set
    case 'm': 
      setMicrosteps(numVal);    // set microstepping mode: 1, 2, 4, 8, 16, 32, 64 and 128 are permitted    
      break;
    case 'o': 
      startDrive(); // engage the drive to carry out a defined number of microsteps     
      break;
    case 'r':
      resetAMIS(); // reset the AMIS via its CLR pin
      break;
    case 's': 
      setSteps(numVal); // set the number of steps to be carried out
      break;
    case 'v': 
      setVelocity(numVal); // set maximum speed in msteps/s      
      break;
    case 'x': 
      stopDrive(); // stop drive
      break;
    case 'z':
      resetCounter(); // set position of stepper to zero
      break;
    default:
      break;
    }
    accelStepper.run();
  }

  driveParams.stepsDone = driveParams.steps - accelStepper.distanceToGo(); // update the current position
  accelStepper.run();
  if (accelStepper.isRunning() == false) {   // check if drives are moving - if they just stopped, disable them ...
    driveParams.isActive = false;
  } 
}

//----------------------------------------------------------------------------------
// respond with an identifier for the drive when receiving the <ACK> character

inline void replyWithDriveID(void) {
  Serial.write("TSC_DE");
}

//----------------------------------------------------------------------------------
// enable the driver without moving it

inline void enableDrive(long enableDrive) {
  if (enableDrive == 1) {
    stepper.enableDriver();
    Serial.write("Stepper enabled");
  } else {
    stepper.disableDriver();    
    Serial.write("Stepper disabled");
  }
}

//-----------------------------------------------------------------------------------
// set acceleration in msteps/(s*s)

inline void setAcc(long acceleration) {

  if ((acceleration > 0) && (acceleration < 100000)) {
    driveParams.acceleration = acceleration;
    accelStepper.setAcceleration(driveParams.acceleration);
    Serial.write("Acceleration set");
  } else {
    Serial.write("Acceleration value not permitted");
  } 
}

//------------------------------------------------------------------------------------
// set stepper counter to home position; speed needs to be reset then

inline void resetCounter(void) {

  accelStepper.setCurrentPosition(0);
  accelStepper.setMaxSpeed(driveParams.maxSpeedInMicrosteps);
  Serial.write("Counter reset");
}

//------------------------------------------------------------------------------------
// set microstepping ratio

inline void setMicrosteps(long ratio) {

  stepper.setCurrentMilliamps(((uint16_t)driveParams.current));
  switch(ratio) {
    case 1: driveParams.stepMode = 1; stepper.setStepMode((uint8_t)driveParams.stepMode); break;
    case 2: driveParams.stepMode = 2; stepper.setStepMode((uint8_t)driveParams.stepMode); break;   
    case 4: driveParams.stepMode = 4; stepper.setStepMode((uint8_t)driveParams.stepMode); break; 
    case 8: driveParams.stepMode = 8; stepper.setStepMode((uint8_t)driveParams.stepMode); break;
    case 16: driveParams.stepMode = 16; stepper.setStepMode((uint8_t)driveParams.stepMode); break; 
    case 32: driveParams.stepMode = 32; stepper.setStepMode((uint8_t)driveParams.stepMode); break;
    case 64: driveParams.stepMode = 64; stepper.setStepMode((uint8_t)driveParams.stepMode); break;
    case 128: driveParams.stepMode = 128; stepper.setStepMode((uint8_t)driveParams.stepMode); break;    
    default: Serial.write("Invalid microstep parameter"); return;
  }
  if (stepper.verifySettings() == true) {
    Serial.write("Microsteps set. AMIS settings ok");  
  } else {
    Serial.write("Microsteps set. Error in AMIS settings");  
  }
}

//------------------------------------------------------------------------------------
// set maximum speed in msteps/s

inline void setVelocity(long sspeed) {
  
  if ((sspeed >= 0) && (sspeed < 100000)) {
    driveParams.maxSpeedInMicrosteps = sspeed;
    accelStepper.setMaxSpeed(driveParams.maxSpeedInMicrosteps);  
    Serial.write("Speed set");
  } else {
    Serial.write("Speed value not permitted");
  } 
}

//-------------------------------------------------------------------------------------
// set number of steps to be carried out. this does not start the drive.

inline void setSteps(long ssteps) {
  
  driveParams.steps = ssteps;
  Serial.write("Steps set");
}

//-------------------------------------------------------------------------------------
// stop the drive: the de-acceleration ramp is carried out

inline void stopDrive(void) {
    accelStepper.stop();
    Serial.write("Drive stopped");
}

//-------------------------------------------------------------------------------------
// start the drive to carry out a defined number of steps

inline void startDrive(void) {
  
  stepper.enableDriver();
  accelStepper.setCurrentPosition(0);
  accelStepper.moveTo(driveParams.steps);
  driveParams.isActive = true;
  Serial.write("Drive started");
}

//-------------------------------------------------------------------------------------
// set the maximum current per coil in milliAmpere; maximum value is 3 A

inline void setCurrent(long curr) {
  
  if ((curr > 10) && (curr < 3000)) {
    driveParams.current = curr;
  //  stepper.setCurrentMilliamps(((uint16_t)driveParams.current));
    delay(50);
    if (stepper.verifySettings() == true) {
      Serial.write("Current set. AMIS settings ok");  
    } else {
      Serial.write("Current set. Error in AMIS settings");  
    }
  } else {
    Serial.write("Current value not permitted");
  }
}

//-------------------------------------------------------------------------------------
// report the condition of the driver

inline void reportAMISStates(long what) {

  accelStepper.run();
  switch(what) {
  case 0: // report whether drive is moving
    if (driveParams.isActive == true) {
      Serial.write('1');
    } else {
      Serial.write('0');
    }
    break;
  case 1: // report the state of the internal ERR pin of the AMIS
    if (digitalRead(amisErrPin) == HIGH) {
      Serial.write("1"); 
    } else {
      Serial.write("0");
    }
    break;
    case 2: // report whether the settings are correct as set on the AMIS via SPI
    if (stepper.verifySettings() == true) {
      Serial.write("1");  
    } else {
      Serial.write("0");  
    }
    break;
    case 5: // report current number of microsteps carried out
        sprintf(outputString,"%ld",driveParams.stepsDone);
        accelStepper.run();
        Serial.write(outputString);    
      break;
    case 6: // report the microstepping ratio
      sprintf(outputString,"%d",driveParams.stepMode);
      accelStepper.run();
      Serial.write(outputString);    
      break;
    case 7: // report the maximum speed in microsteps/s
      sprintf(outputString,"%ld",driveParams.maxSpeedInMicrosteps);
      accelStepper.run();
      Serial.write(outputString);    
      break;  
    case 8: // report the acceleration in microsteps/(s*s)
      sprintf(outputString,"%ld",driveParams.acceleration);
      accelStepper.run();
      Serial.write(outputString);    
      break;  
    case 9: // report the maximum coil current in millAmpere
      sprintf(outputString,"%d",(int)driveParams.current);
      accelStepper.run();
      Serial.write(outputString);    
      break;    
    case 10: // report steps set
     sprintf(outputString,"%ld",driveParams.steps);
      accelStepper.run();
      Serial.write(outputString);    
      break;     
    default: 
      accelStepper.run();
      Serial.write("-1");
      break;  
  }
  accelStepper.run();
  outputString[0] = '\0';
}

//--------------------------------------------------------------------------------------
// sets the CLR pin of the AMIS to HI for 0.5 seconds and resets the buffer of the AMIS

inline void resetAMIS(void) { 
  digitalWrite(resetPin, HIGH);
  delay(500);
  digitalWrite(resetPin, LOW);  
  delay(10);
  stepper.resetSettings();
  stepper.setCurrentMilliamps(driveParams.current);
  stepper.setStepMode(driveParams.stepMode);
  Serial.write("1");
  
}

//---------------------------------------------------------------------------------------

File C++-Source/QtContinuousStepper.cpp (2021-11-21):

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
//---------------------------------------------------
#include "QtContinuousStepper.h"
#include <stdlib.h>
#include <unistd.h>
#include "tsc_globaldata.h"
#include "usb_communications.h"
#include <math.h>
#include <QDebug>

extern TSC_GlobalData *g_AllData;
extern usbCommunications *amisInterface;

QtContinuousStepper::QtContinuousStepper(void){

    this->sendCommandToAMIS("e",1); // enable steppers
    this->hBoxSlewEnded=false;
    this->isHBoxSlew = false;
    this->stopped=true;
    this->gearRatio = 1;
    this->microsteps = 2;
    qDebug() << "Called Right Ascension constructor";
}

//-----------------------------------------------------------------------------

QtContinuousStepper::~QtContinuousStepper(void){
    this->stopped=true;
    this->sendCommandToAMIS("x"); // stop steppers
    this->sendCommandToAMIS("e",0); // disable steppers
}

//-----------------------------------------------------------------------------
void QtContinuousStepper::setGearRatioAndMicrosteps(double gr, double ms) {
    long lms;

    this->gearRatio=gr;
    lms = (long)ms;
    if ((lms != 4) && (lms != 8) && (lms != 16) && (lms != 32) && (lms != 64) && (lms != 128) && (lms != 256)) {
        lms = 16;
    }
    this->sendCommandToAMIS("x"); // stop steppers
    this->sendCommandToAMIS("m",lms);
    usleep(50);
    this->microsteps=lms;
}

//-----------------------------------------------------------------------------
// this routine changes the microstepping ration; for the phidget drivers, it has no effect
void QtContinuousStepper::changeMicroSteps(double ms) {
    long lms;

    lms = (long)ms;
    if ((lms != 4) && (lms != 8) && (lms != 16) && (lms != 32) && (lms != 64) && (lms != 128) && (lms != 256)) {
        lms = 16;
    }
    this->sendCommandToAMIS("x"); // stop steppers
    this->sendCommandToAMIS("m",lms);
    usleep(50);
    this->microsteps=lms;
}

//-----------------------------------------------------------------------------

void QtContinuousStepper::setInitialParamsAndComputeBaseSpeed(double lacc, double lcurr) {
    double amax;

    amax = 20000;
    if (lacc > amax) {
        this->acc = amax;
    } else {
        this->acc = lacc;
    }
    if (lcurr <= 3) {
        this->currMax=lcurr;
    } else {
        this->currMax = 3;
    }
    this->sendCommandToAMIS("a", this->acc);
    this->sendCommandToAMIS("c",(long)(this->currMax*1000));
    usleep(100);
    this->stepsPerSecond=round(g_AllData->getCelestialSpeed()*(this->gearRatio)*(this->microsteps));
    if (this->stepsPerSecond < 1) {
        this->speedMax = 1; // a speed of less than 1 microsteps is not achievable - it is physics, baby ...
        this->stepsPerSecond = this->speedMax;
    }
    this->speedMax=this->stepsPerSecond;
    this->sendCommandToAMIS("v",(long)(this->speedMax));
}

//----------------------------------------------
void QtContinuousStepper::startTracking(void) {

    this->speedMax=g_AllData->getCelestialSpeed()*(this->gearRatio*this->microsteps);
    this->sendCommandToAMIS("v",this->speedMax);
    this->sendCommandToAMIS("z");
    this->sendCommandToAMIS("s", this->RADirection*(60*60*24*this->stepsPerSecond));
    this->sendCommandToAMIS("o");
    this->stopped = false;
}

//-----------------------------------------------
void QtContinuousStepper::travelForNSteps(long steps,short direction, int factor, bool isHBSlew) {

    this->hBoxSlewEnded = false;
    this->isHBoxSlew = isHBSlew;
    this->speedMax=round(factor*g_AllData->getCelestialSpeed()*(this->gearRatio)*(this->microsteps));
    qDebug() << this->speedMax;
    qDebug() << this->microsteps;

    if (direction < 0) {
        direction = -1;
    } else {
        direction = 1;
    }
    this->sendCommandToAMIS("v",this->speedMax);
    this->sendCommandToAMIS("z");
    this->sendCommandToAMIS("s",this->RADirection*direction*steps);
    this->sendCommandToAMIS("o");
    this->stopped = false;
}

//-----------------------------------------------
void QtContinuousStepper::travelForNSteps(short direction, float factor) {

    this->speedMax=round(factor*g_AllData->getCelestialSpeed()*(this->gearRatio)*(this->microsteps));
    if (direction < 0) {
        direction = -1;
    } else {
        direction = 1;
    }
    this->sendCommandToAMIS("v",this->speedMax);
    this->sendCommandToAMIS("z");
    this->sendCommandToAMIS("s",this->RADirection*direction*1000000000);
    this->sendCommandToAMIS("o");
    this->stopped = false;
}

//-----------------------------------------------
void QtContinuousStepper::travelForGuide(float speed, bool startCorrMotion) {
    if (startCorrMotion == true) {
        this->speedMax = speed;
    } else {
        this->speedMax = round(g_AllData->getCelestialSpeed()*(this->gearRatio)*(this->microsteps));
    }
    this->sendCommandToAMIS("v",this->speedMax);
}

//-----------------------------------------------
void QtContinuousStepper::resetSteppersAfterStop(void) { // this function is called once it was detected that the steppers stopped moving
    this->stopped = true;
    this->speedMax=g_AllData->getCelestialSpeed()*(this->gearRatio)*(this->microsteps);
    this->sendCommandToAMIS("v",(long)(this->speedMax));
    if (this->isHBoxSlew == true) {
        this->hBoxSlewEnded=true;
        this->isHBoxSlew = false;
    }
}

//-----------------------------------------------
void QtContinuousStepper::setRADirection(short dir) {
    if (abs(dir) == 1) {
        this->RADirection = dir;
    }
}

//-----------------------------------------------------------------------------
double QtContinuousStepper::getKineticsFromController(short whichOne) {
    double retval = 0;

    switch (whichOne) {
    case 1:
        retval = (double)(this->sendCommandToAMIS("f9").toLong()/1000.0);
        break;
    case 2:
        retval = (double)(this->sendCommandToAMIS("f8").toLong());
        break;
    case 3:
        retval = (double)(this->sendCommandToAMIS("f7").toLong());
        break;
    case 4:
        retval = (this->speedMin);
        break;
    default:
        retval=-1;
    }
    return retval;
}


//-----------------------------------------------------------------------------
bool QtContinuousStepper::getErrorFromDriver(void) {
    double retval;

    retval = (double)(this->sendCommandToAMIS("f1").toLong());
    if (round(retval) == 0) {
        return true;
    } else {
        return false;
    }

}
//-----------------------------------------------------------------------------
void QtContinuousStepper::hwResetDriver(void) {

    //this->sendCommandToAMIS("r");
}
//-----------------------------------------------------------------------------
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

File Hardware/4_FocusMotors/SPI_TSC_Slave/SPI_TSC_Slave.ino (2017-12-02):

// arduino sketch for driving the auxiliary focuser drives of TSC - runs with the hardware from Motorboard.fzz. W. Birkfellner 2017
#include <SPI.h>
#include <AccelStepper.h>
#include <stdlib.h>

AccelStepper aux1Stepper(AccelStepper::DRIVER,3,2); // pin 3 connected to STEP, pin 2 connected to DIR
AccelStepper aux2Stepper(AccelStepper::DRIVER,5,4); // pin 5 connected to STEP, pin 4 connected to DIR
char readCommand;
short sign;
struct kinematicParametersStruct {
  long steps;
  long maxSpeed;
  long acceleration;
  bool isActive;
};

struct kinematicParametersStruct aux1DriveParams; 
struct kinematicParametersStruct aux2DriveParams;

char buf[32];
volatile byte pos;
volatile boolean process_it;
const bool showDebug = false; // if set to false, serial output is supressed ... good for performance
const char whatDriver = 'A'; // this is just a constant that states which driver is connected. it is also sent as a reply when drives are inactive 
// possible values are 'D' for the DRV 8825 or 'A' for the a4988
char reply;

//--------------------------------------------------------------

void setup (void) {
  if (showDebug == true) {
    Serial.begin (115200); 
  }
  pinMode(8,OUTPUT); // connected to M0
  pinMode(7,OUTPUT); // connected to M1 
  pinMode(6,OUTPUT); // connected to M2 of the drv 8825 - sets microstepping for both drives
  digitalWrite(8,HIGH);
  digitalWrite(7,HIGH);    
  digitalWrite(6,LOW); // LLL=full, HLL=half,LHL=1/4,HHL=1/8,LLH=1/16,HLH=LHH=HHH=1/32 for the DRV8825
                       // LLL=full, HLL=half,LHL=1/4,HHL=1/8,HHH=1/16 for the A4998
  pinMode(A0,OUTPUT); // connected to ENABLE pin of drive 1
  pinMode(A1,OUTPUT); // connected to ENABLE pin of drive 2
  digitalWrite(A0,HIGH);
  digitalWrite(A1,HIGH);
  
  aux1DriveParams.steps = 5000;
  aux1DriveParams.maxSpeed = 500;
  aux1DriveParams.acceleration = 500; 
  aux1DriveParams.isActive = false; 
  aux2DriveParams.steps = 5000;
  aux2DriveParams.maxSpeed = 500;
  aux2DriveParams.acceleration = 500;
  aux2DriveParams.isActive = false;   
  aux1Stepper.setMaxSpeed(aux1DriveParams.maxSpeed); 
  aux1Stepper.setAcceleration(aux1DriveParams.acceleration); 
  aux2Stepper.setMaxSpeed(aux2DriveParams.maxSpeed); 
  aux2Stepper.setAcceleration(aux2DriveParams.acceleration); 
  
  pinMode(MISO, OUTPUT); // have to send on master in, *slave out*
  SPCR |= _BV(SPE);  // turn on SPI in slave mode
  pos = 0;   // buffer empty
  process_it = false;
  SPI.attachInterrupt();   // now turn on interrupts
}  

//--------------------------------------------------------------

void loop (void) { // main loop - wait for flag set in interrupt routine
long numVal;
short bCounter;

  aux1Stepper.run();
  aux2Stepper.run();
  if (process_it) { // got a string via SPI - process it accordingly
    pos = 0;
    readCommand=buf[0];
    process_it = false;
    switch (readCommand) {
      case 'e': // enable drives 1 or 2
        enableDrive(buf[1],buf[2]); 
        break;
      case 'a': // set acceleration for drive 1 or 2
        numVal = convertBufToLParam(); 
        setAcc(buf[1],numVal);       
        break;
      case 'm': // set microstepping rate for drive 1 or 2 
        numVal = convertBufToLParam();
        setMicrosteps(numVal);        
        break;
      case 'v': // set velocity for drive 1 or 2
        numVal = convertBufToLParam();
        setVelocity(buf[1],numVal);       
        break;
      case 's': // set steps for drive 1 or 2
        numVal = convertBufToLParam();
        setSteps(buf[1],numVal);       
        break;
      case 't': // if the master wants to know whether there is a slave connected, it sends 't'
        if (showDebug == true) {
          Serial.println("Ping received");
        }        
        break;
      case 'x': // stops drive 1 or 2 
        stopDrive(buf[1]);       
        break;
      case 'o': 
        startDrive(buf[1]);      
        break; 
    }
    for (bCounter = 0; bCounter < 32; bCounter++) {
      buf[bCounter]='#';
    }
  }
  
  // check if drives are moving - if they just stopped, disable them ...
  if ((aux1DriveParams.isActive == true) &&  (aux1Stepper.isRunning() == false)) {
    aux1DriveParams.isActive = false;
    enableDrive('0','0');
  }
  if ((aux2DriveParams.isActive == true) &&  (aux2Stepper.isRunning() == false)) {
    aux2DriveParams.isActive = false;
    enableDrive('1','0');
  }
  
  // set the reply via SPI in dependence of the drives active; if both are inactive, the "whatDriver" constant is returned
  reply = whatDriver;
  if ((aux1DriveParams.isActive == true) && (aux2DriveParams.isActive == true)) {
    reply = 'B';
  } else {
    if (aux1DriveParams.isActive == true) {
      reply = '0';
    }
    if (aux2DriveParams.isActive == true) {
      reply = '1';
    }
  }
  if (showDebug == true) {
    Serial.print("Current reply: ");
    Serial.println(reply);
  }  
} // end of loop

//--------------------------------------------------------------

ISR(SPI_STC_vect) { // SPI interrupt routine
byte c = SPDR;  // grab byte from SPI Data Register

  SPDR=reply;
  if (pos < sizeof buf) {
    if (c != 0x00) {     
      buf [pos++] = c;
    } else {
      buf [pos++] = 0x00;
      process_it = true;
    }
  }  
}    

//--------------------------------------------------------------

long convertBufToLParam(void) { //makes a long out of the buffer starting from pos 2 ...
  long param;
  char subBuf[29];
  char sChar;
  short bCounter=2;

  do {
    sChar=buf[bCounter];
    subBuf[bCounter-2]=sChar;
    bCounter++; 
  } while (sChar != '\0');
  param = strtol(subBuf,NULL, 10);
  return param;
}

//--------------------------------------------------------------

void enableDrive(char whatDrive, char setEnabled) { // reacts to "exy" where x is 0/1 in dependence of the drive, and y is a boolean
  if (showDebug == true) {
    Serial.println("Enable drive ");
    Serial.print(whatDrive);
    Serial.print(" ");
    Serial.println(setEnabled);
    Serial.println ("--------");
  }
  if (whatDrive == '0') {
    if (setEnabled == '1') {
      digitalWrite(A0,LOW);
    } else {
      digitalWrite(A0,HIGH);
    }
  } else { 
    if (setEnabled == '1') {
      digitalWrite(A1,LOW);
    } else {
      digitalWrite(A1,HIGH);
    }
  }  
}
  
//--------------------------------------------------------------

void setAcc(char whatDrive, long value) { // reacts to axy, where x is 0/1 - the drive, ynd y is a string representing a long - the acceleration in microsteps/(s*s)
  if (showDebug == true) {
    Serial.print("Set Acceleration ");
    Serial.print(whatDrive);
    Serial.print(" ");
    Serial.println(value);
    Serial.println ("--------");
  }
  if (whatDrive == '0') {
    aux1DriveParams.acceleration = value;  
    aux1Stepper.setAcceleration(aux1DriveParams.acceleration); 
  } else {
    aux2DriveParams.acceleration = value;
    aux2Stepper.setAcceleration(aux2DriveParams.acceleration); 
  }
}
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

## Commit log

2017-04-30 Initial list of parts for assembling TSC
    Includes parts numbers for the Raspberry Pi, the optional display, the HW-clock, the USB-converter and Phidgets or possible alternative drivers such as the RAPS 128 or the DRV8825 ...
    [TSC_PartsList.xls]
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2017-05-06 Added meridian flip and lunar/solar tracking rates
    [QtContinuousStepper.cpp, QtKineticStepper.cpp, tsc_globaldata.cpp]
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2017-05-07 Updated parts list
    [TSC_PartsList.xls]
2017-05-07 Just a few GUI changes
    [TSC_PartsList.xls]
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2017-05-18 Added schematics for hardware
    [TSC_PartsList.xls]
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2017-05-22 Small changes in the BT-connection
    [TSC_PartsList.xls]
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2017-09-06 Fritzing file for mini-handbox
    Fritzing file incl. PCB layout for the bluetooth handbox based on an Arduino Pro Mini
    [Handbox.fzz]
2017-09-07 First draft of Hat-PCB
    A first and unverified design for a TSC - Hat containing USB/Serial, Realtime - Clock, ST4 and DSL Interface, a fan and a few pinouts,
    [TSC_Hat.fzz]
2017-09-08 Updated Pi HAT
    [TSC_PiHat.fzz]
2017-09-08 small updates in routing
    [TSC_PiHat.fzz]
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2017-09-10 Changed connections for easy soldering
    [TSC_PiHat.fzz]
2017-09-12 New version of the Fritzing file for the Pi-HAT
    Routing optimized, SMD footprint for the ADuM added ...
    [TSC_PiHat_SMD_ADuM.fzz]
2017-09-12 Small changes to PCB
    [TSC_PiHat_SMD_ADuM.fzz]
2017-09-12 Small PCB optimizations
    [TSC_PiHat_SMD_ADuM.fzz]
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2017-09-14 Fine Tuning of PCB
    [TSC_PiHat_SMD_ADuM.fzz]
2017-09-18 Redesigned PCB
    [TSC_PiHat_SMD_ADuM.fzz]
2017-09-18 Schematic cleared
    [TSC_PiHat_SMD_ADuM.fzz]
2017-09-18 PCB optimizations
    [Handbox.fzz]
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2017-09-18 PCB optimized
    [Handbox.fzz]
2017-09-19 Added Diode to avoid frying the Arduini
    [Handbox.fzz]
2017-09-21 BT-MAC address ...
    ... is now saved in a separate file
    [Handbox.fzz]
2017-09-28 changed directory structure
    [Handbox.fzz, TSC_PartsList.xls, TSC_PiHat_SMD_ADuM.fzz]
2017-10-03 Slight revision of PCB drillholes
    [TSC_PiHat_SMD_ADuM.fzz]
2017-10-03 Part list updated
    [TSC_PartsList.xls]
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2017-10-25 uploaded a new motorboard design
    new motorboard design (fritzing file, updated motorsketch
    [MotorBoard.fzz]
2017-10-26 removed PWR out
    ... as it does not provide too much current and makes little sense
    [TSC_PiHat_SMD_ADuM.fzz]
2017-10-26 added a fuckin' verpolungsschutz
    [Handbox.fzz]
2017-11-06 draft for a teensy controlled 4 drive board added ...
    [Bigger4DriveBoard.fzz]
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2017-11-13 fianl fritzing and arduino sketches for handbox and focus motors added
    [Handbox.fzz, MotorBoard.fzz]
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2017-11-16 added a final Fritzing file for the 4DrvBoard
    [TSC_PiHat_SMD_ADuM.fzz]
2017-11-20 sub-circuit for dslr added
    a samll fritzing for the optically decoupled dslr jack
    [TSC_Camera_JackV2.fzz]
2017-11-20 removed divider for motorboard
    [MotorBoard.fzz]
2017-11-21 new draft for HAT
    [TSC_PiHat_ILD.fzz]
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2017-11-21 draft vor HAT V1.2
    [TSC_PiHat_ILD.fzz]
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2017-11-30 Changed HAT pcb completely
    [TSC_PiHat_ILD.fzz]
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2017-11-30 >Slight revisions on the focusmotorboard
    [MotorBoard.fzz]
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2017-12-02 added an analog input for temperature
    [MotorBoard.fzz]
2017-12-02 slicght handbox PCB modifications
    [Handbox.fzz]
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2017-12-05 4 Drv Board PCB corrected
    [Bigger4DriveBoardV1.1.fzz]
2017-12-05 4 Drv PCB corrected
    [Bigger4DriveBoardV1.1.fzz]
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2017-12-19 Slight correction to Quad Motor Board
    [Bigger4DriveBoardV1.1.fzz]
2017-12-19 PCB Corrections added
    [Bigger4DriveBoardV1.1.fzz]
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2017-12-22 New HAT PCB uploaded
    [TSC_PiHat_ILD_V1_4.fzz]
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2017-12-24 Modified Focus Motor PCB
    [MotorBoard.fzz]
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2017-12-24 slight corrections in PCB schematic
    [MotorBoard.fzz]
2017-12-26 added a new handbox version with focuser ctrl
    [HandboxV1_2.fzz]
2017-12-29 redesigned 10switch PCB
    [HandboxV1_2.fzz]
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2018-01-06 small bugfixes in autoguider calibration
2018-01-18 changed labels on PCB
    This HAT works fine!!!
    [TSC_PiHat_ILD_V1_4.fzz]
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2018-02-04 decl-backlash and dithering added
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2018-02-20 Fritzing for the TCP/IP handbox with an Adafruit Feather ES32
    [TCP_Handbox.fzz]
2018-02-22 cleaned up schematic for TCP handbox
    [TCP_Handbox.fzz]
2018-02-25 changed labels on PCB
    [TSC_PiHat_ILD_V1_4.fzz]
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2018-02-27 added a few bugfixes
    [tsc_globaldata.cpp]
2018-03-07 fixed a bug in gear speeds
2018-03-09 changed an error in PCB lettering
    [TCP_Handbox.fzz]
2018-03-11 fixed a route on PCB
    [TCP_Handbox.fzz]
2018-03-11 cleaned up the directory structure
    [TCP_Handbox.fzz]
2018-03-19 added a breakout board for 6 RJ12 connectors
    [ConnectorBreakout.fzz]
2018-03-26 added a lowpass filter for autoguider corrections
2018-03-29 a little experimental design to add GPS to the HAT
    [TSCMobile_PiHat_ILD_V1.0.fzz]
2018-04-02 added bugfixes, mainly related to autoguiding
    [spi_drive.cpp]
2018-05-01 a version of the TSC HAT with a connector for GPS
    This is an enhancement of the HAT V. 1.4 - TX/RX and Power/Ground lines were added for connecting a Adafruit Ultimate GPS Breakout V3 to the Arduino Pro Mini mounted to the HAT. The Arduino can reque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
    [TSC_PiHat_ILD_V1_5.fzz]
2018-05-01 added a few components to the BOM
    [TSC_PartsList.xls]
2018-05-22 corrected the BOM
    [TSC_PartsList.xls]
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2018-09-01 added a few fixes before driver change
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2018-10-07 fixed a race condition in the constructor of mainwindow
    [QtKineticStepper.cpp, tsc_globaldata.cpp]
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2018-10-07 bug on the PCB removed
    short circuit with RTC battery case and a via was removed
    [TSC_PiHat_ILD_V1_5.1.fzz]
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2019-01-02 New Board for the Teensy Microcontroller family
    [AMIS30543_Teensy.fzz]
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2019-04-23 Corrected Powerlines for stepper
    [AMIS30543_Teensy_1_3.fzz]
2019-04-23 Updated TSC for AMIS drivers: motion works
    update for AMIS drivers
    - Motion, Handbox, GoTo, Parking and LX200 work
    - missing: ST4, autoguiding, meridian flip
    [QtContinuousStepper.cpp, QtKineticStepper.cpp]
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2019-11-19 handled the polar crossing hopefully
    ... don't try the meridian flip for GEMs!
    [QtContinuousStepper.cpp, QtKineticStepper.cpp, tsc_globaldata.cpp]
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2019-11-25 Modified the HAT
    ... by removing the fan. A fan can also be included in the encasement.
    [TSC_PiHat_ILD_V1_5.2.fzz]
2019-11-25 Uploaded new PCB versions...
    for the HAT without a fan and for a single motor driver PCB featuring 2 Teensy 4.0s ...
    [AMIS30543_Teensy_1_3.fzz, AMIS30543_Teensy_2.fzz, Bigger4DriveBoardV1.1.fzz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]
2019-11-26 Finalized the meridian flip ...
    [tsc_globaldata.cpp]
2019-11-27 smaller HAT PCB updated
    [TSC_PiHat_ILD_V1_5.2.fzz]
2019-11-28 added a layout for a handbox with the wemos lolin D32
    [TCP_Handbox.fzz]
2019-12-02 mad minor PCB adjustments
    [AMIS30543_Teensy_2.fzz]
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2019-12-17 USB error handling improved
    [tsc_globaldata.cpp]
2019-12-31 refinded meridian flip criteria
    [tsc_globaldata.cpp]
2020-01-10 refined meridian flip criteria,
    added handbox motion controls, and a periodic check for hardware errors ...
    [QtContinuousStepper.cpp, QtKineticStepper.cpp]
2020-01-23 fixed ground issue on RTC
    [TSC_PiHat_ILD_V1_5.3.fzz]
2020-01-23 updated gerber files for 1.5.3
    [TSC_PiHat_ILD_V1_5.2_contour.gm1, TSC_PiHat_ILD_V1_5.2_copperBottom.gbl, TSC_PiHat_ILD_V1_5.2_copperTop.gtl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]
2020-02-03 slight updates in hardware
    [AMIS30543_Teensy_1_3.fzz, AMIS30543_Teensy_4.fzz, MotorBoard.fzz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]
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2023-05-12 New PCB Layout with GPS Chip
    [AMIS30543_Teensy_4.fzz]

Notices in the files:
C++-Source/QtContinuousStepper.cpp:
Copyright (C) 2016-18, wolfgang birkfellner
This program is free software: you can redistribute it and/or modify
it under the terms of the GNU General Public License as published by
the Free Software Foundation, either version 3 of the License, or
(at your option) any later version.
